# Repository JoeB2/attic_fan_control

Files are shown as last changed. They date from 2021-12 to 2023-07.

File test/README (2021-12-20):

This directory is intended for PlatformIO Unit Testing and project tests.

Unit Testing is a software testing method by which individual units of
source code, sets of one or more MCU program modules together with associated
control data, usage procedures, and operating procedures, are tested to
determine whether they are fit for use. Unit testing finds problems early
in the development cycle.

More information about PlatformIO Unit Testing:
- https://docs.platformio.org/page/plus/unit-testing.html

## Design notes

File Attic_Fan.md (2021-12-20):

Problem:
Turn on/off attic fan in the summer.  Use attic temp, Web Page, and outside sensor to determine whether fan is on or off.

Considerations:
Fan On/Off (use 5min increment timmer)

Fan on if Attic above some threshold temp : 110f

Fan never on - inside temp <75 and Delta Inside-Outside > 20

Fan on if delta inside-outside > 10f
Fan on if delta attic-outside > 50f

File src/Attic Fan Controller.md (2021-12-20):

## Introduction

This ESP8266 web based application is intended to allow a user to set temperature difference thresholds, between 3 temperature probes, which will determine whether the attic fan will turn on or off.

## Architecture

The ESP8266 is an ESP01-1M.  The MCU hosts four web pages, readings, settings, wifi, and OTA (Over the Air firmware updates).  WebSockets are used to manage communication between the MCU and the web pages.  Web pages are hosted on the user's local wifi network, using provided ip4 and ssid/password information using the wifi web form.  Additionally the MCU simultaneously hosts an access point ("AtticFan WiFi: 10.0.1.23") on a fixed ip at 10.0.1.23.  The access point allows the user to set ip4 information for the local wifi network, read sensor and fan status values, set fan activation thresholds, and update the firmware over wifi - the same as the local WiFi ip would.  The Attic and inside temperature probes are dallas DS18B20 probes using the "one wire" protocol.  The outside probe is a BME280 using the i2c protocol and it transmits its values using the proprietary ESPNOW protocol.  Rem,ote sensor values are sent every "Remote Sensor Check-In Minutes" which is configurable on the setting web page.

Threshold and wifi values are stored in non volatile memory using JSON strings.  The string format is as follows:

### atticFan JSON:
***[{"t1":75.2,"t2":75.4,"t3":74.6,"p3":29.25,"h3":32,"dp3":42,"a3":1448,"vcc":3.0,"atticEpochTime":1638658867,"fanOn":false,"fanOnMs":96},{"attic_on":150,"attic_off":0,"AID_on":0,"AID_off":0,"AOD_on":0,"AOD_off":0,"IOD_on":7,"IOD_off":3,"fanEnabled":false,"delayMs":0,"sleepTIMEus":15000000}]***

###  WiFi JSON:
***{"ssid":"mySSID","pwd":"myPassword","isDHCP":false,"ip":"10.9.8.07","gw":"10.9.8.128","mask":"255.255.255.128"}***

The JSON strings can me modified using the associated web pages and uploaded over the connected wifi network.  

## Operation
  Network Setup
    1) after startup of the attic MCU (micro controller unit) connect to the WiFi access point "AtticFan WiFi: 10.0.1.23".
    2) Point your web browser to: http://10.0.1.23/wifi
        Note: lower case wifi.
    3) Fill out the WiFi settings with the values for your local WiFi network and submit, which will save  the values to non volatile memory (SPIFFS) in a JSON string.
    4) After the WiFi settings are saved the MCU will attempt to re initiate connection to local WiFi provided when filling out the WiFi web form.  An MCU restart is typically not required.

## Home readings web page (http://ip/)

Temperature are provided for all three temperature probes.  The outside probe also provided humidity and barometric pressure reading.  The Attic MCU uses the outside prob's val;ues to calculate outside dew point and density altitude.  The reading page provides "Fan On Timer" values and to disable or active the system.

## Settings (http://ip/settings)

Values are provided using the web form at: http://ip/settings, where ip is the local WiFi ip provided during step 1 of the Network Setup.  Alternatively you can use the Access Point ip, after connecting to the MCU's provided access point.
Settings "AOD, AID, IOD" are value of difference in temperature fahrenheit between temperature probes.  IOD_on (inside - outside = difference) turns on the fan if the difference between the inside temperature probe and the outside temperature probe is equal or greater than the value provided.  Similarly the fan will turn off if: there are no other fan on values whose thresholds have been met and the *inside temp probe* **-** *outside temp probe* **<** ***IOD_off***.  

Order of precedence for automating fan ***on***:
  Fan On:
    - Force Fan On Minutes
    - Fan On Attic Temp
    - IOD on
    - AID on
    - AOD on

Setting "fan System Enabled" to off will disable the fan.
Otherwise IOD off, AOD off, AID off, Attic Fan off temp will be honored with the first threshold met that doesn't conflict with ***any*** fan on threshold turning off the fan.  If no fan off threshold is set the fan will turn off when no "fan On" threshold is met.

Attic Sensor Check-In Seconds setting will change the frequency that the system looks at Attic and Inside temperature probe values and also the frequency that the settings are tested and sent to the web page.

Likewise the "Remote Sensor Check-In Minutes" setting will determine the frequency that the battery operated outside sensor wakes up and transmits the outside temperature.  Battery life will be extended with greater Remote Sensor Check-In values.

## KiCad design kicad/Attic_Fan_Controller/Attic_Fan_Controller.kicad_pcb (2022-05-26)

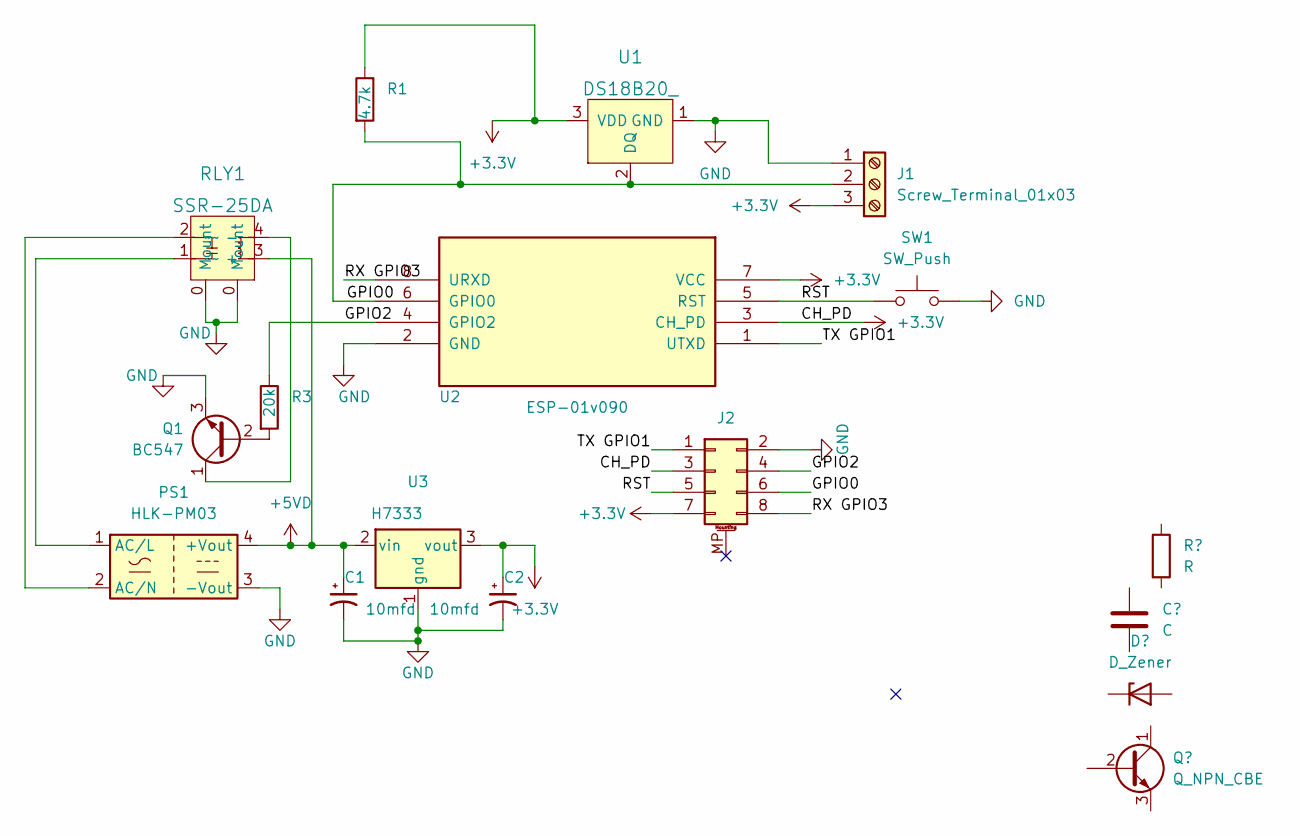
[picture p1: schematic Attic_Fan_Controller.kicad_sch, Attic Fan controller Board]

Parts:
C1, C2: 10mfd; CP_Radial_D4.0mm_P1.50mm
J1: Screw_Terminal_01x03; TerminalBlock_Phoenix_PT-1,5-3-5.0-H_1x03_P5.00mm_Horizontal
J2: Conn_02x04_Odd_Even_MountingPin; PinSocket_2x04_P2.54mm_Vertical
PS1: HLK-PM03; Converter_ACDC_HiLink_HLK-PMxx
Q1: BC547; TO-92_Inline
R1: 4.7k; R_Axial_DIN0207_L6.3mm_D2.5mm_P10.16mm_Horizontal
R3: 20k; R_Axial_DIN0207_L6.3mm_D2.5mm_P10.16mm_Horizontal
RLY1: SSR-25DA; SSR-25 DA; MPN 9007-05-00; Digi-Key_PN 306-1062-ND
SW1: SW_Push; SW_PUSH_6mm_H5mm
U1: DS18B20_; TO-92-3; MPN DS18B20+; Digi-Key_PN DS18B20+-ND
U2: ESP-01v090; ESP-01
U3: H7333; SOT-89-3

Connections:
+3V3: C2.1, J1.3, J2.3, J2.7, R1.1, U1.3 (VDD), U2.3 (CH_PD), U2.7 (VCC), U3.3 (vout); also elsewhere on the board
+5VD: C1.1, PS1.4 (+Vout), RLY1.3 (+), U3.2 (vin)
/GPIO0: J1.2, J2.6, R1.2, U1.2 (DQ), U2.6 (GPIO0)
/GPIO2: J2.4, R3.1, U2.4 (GPIO2); also elsewhere on the board
/RST: J2.5, SW1.1, U2.5 (RST)
/RX GPIO3: J2.8, U2.8 (URXD)
/TX GPIO1: J2.1, U2.1 (UTXD)
GND: C1.2, C2.2, J1.1, J2.2, PS1.3 (-Vout), Q1.3 (E), RLY1.0 (Mount), SW1.2, U1.1 (GND), U2.2 (GND), U3.1 (gnd)
unnamed: PS1.1 (AC/L), RLY1.1 (~~)
unnamed: PS1.2 (AC/N), RLY1.2 (~~)
unnamed: Q1.1 (C), RLY1.4 (-)
unnamed: Q1.2 (B), R3.2

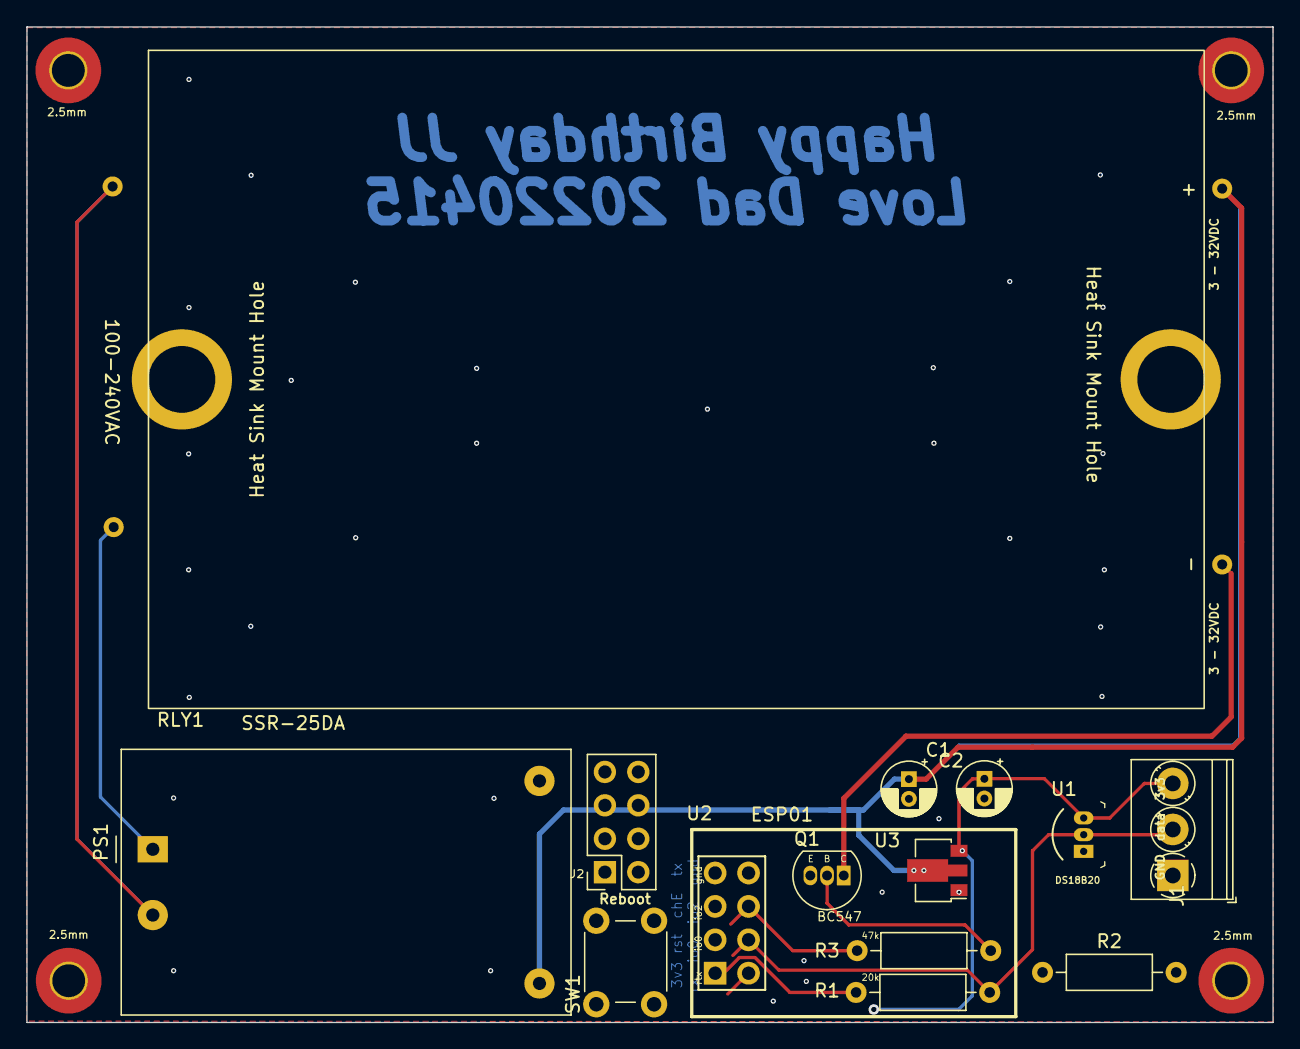
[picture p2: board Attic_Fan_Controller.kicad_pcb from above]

Board: 2 copper layers, 94.7 x 75.7 mm, 18 parts (0 on the bottom side), 12 nets.

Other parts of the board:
2.5mm, 2.5mm#2, 2.5mm#3, 2.5mm#4: MountingHole_2.5mm_Pad_TopBottom
R2: 10k; R_Axial_DIN0207_L6.3mm_D2.5mm_P10.16mm_Horizontal

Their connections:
+3V3: R2.1; also elsewhere on the board
/GPIO2: R2.2; also elsewhere on the board

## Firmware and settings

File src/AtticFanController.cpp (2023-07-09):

#include <Arduino.h>
/*
  Attic Fan Controller

  Purpose:  Regulate an attic fan's on and off.  The fan will move air from the hallway into the attic
            and the attic air will consequently move out of the attic's roof and eves vents.

  What this does: Measurement of attic temperature, hallway temperature, and outside temperature are calculated
            fed into a function to determine whether to turn the fan on or turn the fan off.

  The Fan ON/OFF function: uses the three temperatures (Attic, Inside, Outside) and compares them and
            their differences to values provided by you to automate the attic fan during the hot summer days.

  Function: There are four hosted web pages: 1. Main page http://ip showing status and providing you with a fan override
            function.  2. A settings page http://ip/settings where you can enter temperature difference values that will trigger
            Fan ON/OFF activity.  3. A WiFi settings page http://ip/wifi where local WiFi information can be entered.
            4. A over the air OTA page http://ip/update where firmware or static storage information can be uploaded to
            the ESP01 attic MCU.
            Stored in the MCU's static memory are two JSON strings named: atticFan and creds.  They host the fan's
            operational temperature deltas and the WiFi credential information, respectively.

            A value of zero "0" for a given Fan operational parameter disables that parameter.
  NOTE:     The parameters entered on the http://ip/settings page denote the temperature difference in degrees Fahrenheit.

            example: AOD on value: "Attic Outside Delta on" a value of 10 indicates you want the fan on
            if Attic Temp minus Outside temp is greater than or equal to 10 degrees f.  Absolute temperature settings are
            specifically labeled as such.
            int(4), uint(4), uint32(4), long(4), uLong(4), uLongLong(8), short(2), ushort(2), float(4), double(8)

  Primary Parts:
            ESP8266 - ESP01, 2ea DS18b20, relay, PCB/3.3vdc regulator; 
*/

#define dbg
#ifdef dbg
  u32 ms=millis();
  #define trace Serial.printf("%i %lums, ", __LINE__, millis()-ms);ms=millis();Serial.flush();
#else
  #define trace ;
#endif
#define dbg2

#include <LittleFS.h>
#include <ESP8266WiFi.h>
//#include <WiFiClientSecure.h>
#include <ESP8266mDNS.h>
#include <espnow.h>
#include <string>

// OTA
#include <AsyncElegantOTA.h>

// Web Server
#include <ESPAsyncWebServer.h>
#include <ESPAsyncTCP.h>
#include <index.h>

// DS18B20
#include <OneWire.h>
#include <DallasTemperature.h>

// bit macros
#define SET_BIT(x, pos) (x |= (1U << pos))

#define CLEAR_BIT(x, pos) (x &= (~(1U<< pos)))
#define CHECK_BIT(x, pos) (x & (1UL << pos) )

// Standard settings for compile
#define SSR_PIN 5       // ESP01: 3
#define ALTITUDE 394    // MSL altitude at JJ's house
#define WiFiChannel 7   // ESP NOW requires all peers are on the same channel
#define ONE_WIRE_BUS 4  // ESP01: 0

const char AP_SSID[]   = "AtticFan AP: 10.17.17.23"
         , HOST_NAME[] = "JJ's Attic Fan Controller"; // max length 32

const DeviceAddress // DS18B20 Addresses
          T1={0x28, 0x9C, 0x50, 0xF4, 0x3E, 0x19, 0x01, 0x12}  // white mark : Attic ...0x12
        , T2={0x28, 0x31, 0xCA, 0xC7, 0x3E, 0x19, 0x01, 0xCE}; // Corded     : Inside ...0xCE

// ESPNOW
//u8 peer[]       = {0xFF,0xFF,0xFF,0xFF,0xFF,0xFF};   // MAC: MultiCast"
u8 remote_Mac[]       = {0xDC,0x4F,0x22,0x49,0x59,0x15};   // MAC: MultiCast"

float tSync[] = {-1.2,0.55}; // attic, inside : sync DS18B20 temps to BME280

u32 startMillis=millis(); // loop sensor read delay
u32 last_Remote_Contact_millis=millis(); //

AsyncWebServer webServer(80);
AsyncWebSocket webSock("/");

OneWire oneWire(ONE_WIRE_BUS);
DallasTemperature sensors(&oneWire);

IPAddress  // soft AP IP info
          ip_AP(10,17,1,23)
        , ip_GW(10,17,0,125)
        , ip_AP_GW(10,17,1,23)
        , ip_subNet(255,255,255,128);

  struct {
//      std::string ssid = "myWiFi";     // max 342 characters
//      std::string pwd  = "secretPWD";  // max 64 characters
//      std::string host = HOST_NAME;
//      bool isDHCP      = false;
//      std::string ip   = "198.162.123.117";
//      std::string gw   = "198.162.123.117";
//      std::string mask = "255.255.255.128";
//      bool isDHCP      = false;
      std::string ssid = "JRJAG";     // max 342 characters
      std::string pwd  = "GeorgeTheDogy";  // max 64 characters
      std::string host = HOST_NAME;
      bool isDHCP      = true;
      std::string ip   = "10.137.17.23";
      std::string gw   = "10.137.17.1";
      std::string mask = "255.255.255.128";
      bool updated     = 0;

      std::string toStr(){
        char s[146];
        size_t n;
        n = sprintf(s, "{\"src\":\"mcuNetwork\",\"ssid\":\"%s\",\"pwd\":\"%s\",\"isDHCP\":%hhu,\"ip\":\"%s\",\"gw\":\"%s\",\"mask\":\"%s\",\"updated\":%hhu}"
        , ssid.c_str(), pwd.c_str(), isDHCP?1:0, ip.c_str(), gw.c_str(), mask.c_str(), updated);
        return(std::string(s, n));
      };
  } network;

typedef struct remote_Data{
  int temp;
  u32 press;
  u32 humid;
  u64 sleep_us = 4000000;
  u16 vcc;

  String toStr(){
    char c[120];
    int n = sprintf(c, "{\"temp\":%i,\"press\":%u,\"humid\",:%u,\"vcc:%hu,\"sleep_us\":%llu}"
      , temp, press, humid, vcc, sleep_us);
    c[n]=0;
    return String(c);
  }
}remote_data_t;
remote_data_t now_Msg;

 struct{
  float t1;		                  // attic
  float t2;	                    // inside
  float t3;	                    // outside - remote sensor temp
  u32 p3;                       // outside air pressure inHg
  u32 h3;	                      // humidity outside
  u32 vcc;	                    // battery voltage Vcc at remote sensor
  bool fanOn;	                  // fan on/off indicator
  int fanOnMs=0;         
  byte attic_on;                // Attic temp to force Fan ON: 0 to disable (Master Override)
  byte attic_off;               // Attic temp to turn fan OFF: 0 to dissable
  byte inside_off=70;           // Fan is off if t2 (inside) is below 70 (default) degrees;
  byte AID_on;                  // Attic - Inside temp delta for fan ON: 0 to dissable   (precedence 3)
  byte AID_off;                 // Attic - Inside temp delta for fan OFF: 0 to dissable
  byte AOD_on;                  // Attic - Outside temp delta for fan ON: 0 to dissable  (precedence 2)
  byte AOD_off;                 // Attic - Outside temp delta for fan OFF: 0 to dissable
  byte IOD_on;                  // Inside - Outside temp delta for fan ON: 0 to dissable (precedence 1)
  byte IOD_off;                 // Inside - Outside temp delta for fan OFF: 0 to dissable
  bool systemEnabled;           // true: ok to turn on fan; // logic simplifies some c++ later on
  unsigned long delayMs = 15000;// how often are attic temps checked in milliseconds
  u64 sleep_us = 2*60*1e6+2;    // default: 2mins 2us: remote sensor deepSleep time
  bool updated = false;

    std::string mcuMain(){      // make JSON string: #1 Readings, #2 Settings
      char c[275];
      size_t n;
      n = sprintf(c, "{\"src\":\"mcuMain\",\"t1\":%# 6.1f,\"t2\":%# 6.1f,\"t3\":%# 6.1f,\"p3\":%u,\"h3\":%u,\"vcc\":%hu,\"fanOn\":%hhu,\"fanOnMs\":%i,\"systemEnabled\":%hhd,\"sleep_us\":%llu}"
      , t1, t2, t3, p3, h3, vcc, fanOn?1:0, fanOnMs, systemEnabled?1:0, sleep_us);

      return(std::string(c, n));
    }
    std::string mcuSettings(){ // make JSON string: #1 Readings, #2 Settings
      char c[285];
      size_t n;
      // we send this json using webSock to the settings web page
      n = sprintf(c, "{\"src\":\"mcuSettings\",\"fanOn\":%hhu,\"attic_on\":%hhu,\"attic_off\":%hhu,\"inside_off\":%hhu,\"AID_on\":%hhu,\"AID_off\":%hhu,\"AOD_on\":%hhu,\"AOD_off\":%hhu,\"IOD_on\":%hhu,\"IOD_off\":%hhu,\"systemEnabled\":%hhu,\"delayMs\":%lu,\"sleep_us\":%llu,\"updated\":%hhu}"
      , fanOn?1:0, attic_on, attic_off, inside_off, AID_on, AID_off, AOD_on, AOD_off, IOD_on, IOD_off, systemEnabled?1:0, delayMs, sleep_us, updated);

      return(std::string(c, n));
    }
    // atticFan struct: true==turn on fan
    bool setFanOn(){
        // 1)systemEnabled, 2)timmer, 3)inside_off -> order of precedence
        if(systemEnabled==0){fanOn=0;return 0;}
        if(fanOnMs){fanOn=1;return 1;}
        if(inside_off && t2 <= inside_off){fanOn=0;return 0;}

        // fan OFF tests: is there an off setting that is active?
        if(IOD_off && t2-t3<IOD_off)fanOn=0;
        if(AOD_off && t1-t3<AOD_off)fanOn=0;
        if(AID_off && t1-t2<AID_off)fanOn=0;
        if(attic_off && t1<attic_off)fanOn=0;

        // turn off fan, if there is not an "Off Setting" that has been set else leave as is
        fanOn &= (AID_off | AOD_off | IOD_off | attic_off | inside_off);

        // NOTE: On settings override conflicting (AID, AOD, IOD) temp off settings
        // fanOn ON checks: Should the fan be turned on because of a setting?  else leave as is
        fanOn |= ( (AOD_on&(t1-t3 >= AOD_on)) | (AID_on&(t1-t2 >= AID_on)) | (IOD_on&(t2-t3 >= IOD_on)) | (attic_on&(t1>=attic_on)));
        return fanOn;
    }
  }atticFan;

  /******  PROTOTYPES  *******/
  // web
  void notFound(AsyncWebServerRequest *request);
  void onWsEvent(AsyncWebSocket * server, AsyncWebSocketClient * client, AwsEventType type, void * arg, uint8_t *data, size_t len);

	// ESP_NOW
	void OnDataSent(uint8_t *mac_addr, uint8_t sendStatus);
	void OnDataRecv(uint8_t * mac, uint8_t *incomingData, uint8_t len);

  void initAtticFanStruct(); // load struct atticFan from LittleFS
  void setAtticFanStruct(const std::string &s); // set struct atticFan's differential switching values from WebSock string
  bool saveAtticFanStruct(); // save struct atticFan's JSON string in LittleFS
  bool initWiFi(); // load struct creds from LittleFS
  bool saveWiFi(); // save struct creds JSON string in LittleFS 
  void initWiFi(const std::string &s); // load struct creds from WebSock string
  wl_status_t wifiConnect(WiFiMode_t m);
  IPAddress str2IP(const std::string &s);
  String mac2string(const uint8_t *mac);
  std::string valFromJson(const std::string &json, const std::string &element);// Parse JSON string


  void setup() {
#ifdef dbg
    Serial.begin(74880); // initial boot message is at 74880
    delay(500);
    Serial.printf("\n%i\n", __LINE__);Serial.flush();
#endif
    sensors.begin();
    LittleFS.begin();     // store WiFi Creds
trace
    initWiFi();           // get WiFi credentials from LittleFS
    initAtticFanStruct(); // get temp settings
trace

    wifi_set_phy_mode(PHY_MODE_11B); // high power wifi
    if(wifiConnect(WIFI_STA) != WL_CONNECTED)wifiConnect(WIFI_AP);
		pinMode(SSR_PIN, OUTPUT);
    digitalWrite(SSR_PIN, 0);
trace

		esp_now_init();
		esp_now_set_self_role(ESP_NOW_ROLE_COMBO);
		esp_now_register_send_cb(OnDataSent);
		esp_now_register_recv_cb(OnDataRecv);
		esp_now_add_peer(remote_Mac, ESP_NOW_ROLE_COMBO, WiFiChannel, NULL, 0);
trace

		// init Websock
		webSock.onEvent(onWsEvent);
		webServer.addHandler(&webSock);
trace

		// Web Pages
		webServer.onNotFound(notFound);
    if(WiFi.softAPIP().toString() == "(IP unset)"){
      webServer.on("/"         , HTTP_GET, [](AsyncWebServerRequest *request){request->send_P(200, "text/html", MAIN);});
      webServer.on("/settings" , HTTP_GET, [](AsyncWebServerRequest *request){request->send_P(200, "text/html", SETTINGS);});
      webServer.on("/wifi"     , HTTP_GET, [](AsyncWebServerRequest *request){request->send_P(200, "text/html", NETWORK);});
    }
    else {webServer.on("/"     , HTTP_GET, [](AsyncWebServerRequest *request){request->send_P(200, "text/html", NETWORK);});}

    ESP.wdtFeed();
		AsyncElegantOTA.begin(&webServer);    // Start ElegantOTA
trace
		webServer.begin();
trace
		startMillis=millis()-atticFan.delayMs; // get temps immediately after startup
  }
  void loop() {
    if(millis()-startMillis > atticFan.delayMs){
trace

        sensors.requestTemperatures();
        atticFan.t1 = sensors.getTempF(T1)+tSync[0];
        atticFan.t2 = sensors.getTempF(T2)+tSync[1];
trace

        ESP.wdtFeed();

        /** Timer Section **/
        if(atticFan.fanOnMs)atticFan.fanOnMs-=(millis()-startMillis);
        if(atticFan.fanOnMs>120*60000)atticFan.fanOnMs=120*60000;// 2hr max timer
        if(atticFan.fanOnMs<(int)atticFan.delayMs)atticFan.fanOnMs=0;
        atticFan.setFanOn();
        /** END Timer Section **/

        digitalWrite(SSR_PIN, atticFan.fanOn);
        webSock.textAll(atticFan.mcuMain().c_str());
        ESP.wdtFeed();
trace

        /** LastRemoteContact Section **/
        // if missed last 3 remote contacts set sensor readings to zero
        if(millis() - last_Remote_Contact_millis > 3*atticFan.sleep_us)
        {atticFan.t3=0;atticFan.p3=0;atticFan.h3=0;atticFan.vcc = 0;}
        /** END lastRemoteContact **/

        startMillis=millis();
    }
  }
  void notFound(AsyncWebServerRequest *request){request->send_P(200, "text/html", MAIN);}
  //**********************************************************************
  void onWsEvent(AsyncWebSocket * server, AsyncWebSocketClient * client, AwsEventType type, void * arg, uint8_t *data, size_t len){
    if(type == WS_EVT_CONNECT){client->ping();webSock.cleanupClients();}
    if(type == WS_EVT_DISCONNECT){client->close();webSock.cleanupClients();}
//**************
    if(type != WS_EVT_DATA)return;
      AwsFrameInfo * info = (AwsFrameInfo*)arg;
      if(info->final && !info->index && info->len == len){
        if(info->opcode != WS_TEXT)return;
      }
      data[len]=0; // null terminate the char[]
      std::string s((char*)data, len);
      std::string src = valFromJson(s, "src");
      std::string what = valFromJson(s, "what");

#ifdef dbg
    Serial.printf("\n%i ws_in: %s\n", __LINE__, s.c_str());
#endif
      if(src=="main"){
        if(what=="system"){
          atticFan.systemEnabled = ::atoi(valFromJson(s, "system").c_str());
        }
        if(what=="timer"){
          atticFan.fanOnMs = ::atoi(valFromJson(s, "fanOnMs").c_str());
        }
        atticFan.setFanOn();
        digitalWrite(SSR_PIN, atticFan.fanOn);
        client->text(atticFan.mcuMain().c_str());
      }
      if(src=="settings"){
          if(what=="submit"){
            setAtticFanStruct(s);
            atticFan.updated = saveAtticFanStruct();
          }
          if(what=="system"){
            atticFan.systemEnabled = ::atoi(valFromJson(s, "systemEnabled").c_str());
          }
          digitalWrite(SSR_PIN, atticFan.setFanOn());
#ifdef dbg
  Serial.printf("\n%i %s\n", __LINE__, atticFan.mcuSettings().c_str());
#endif
          client->text(atticFan.mcuSettings().c_str());
          atticFan.updated = false;
        }
      if(valFromJson(s, "src")=="network"){
        if(what=="reboot")ESP.restart();
        if(what=="submit"){
          initWiFi(s); // <-- updated, but no reboot yet
          network.updated = saveWiFi();
        }
        client->text(network.toStr().c_str()); // include "updated" value
      }
#ifdef dbg2
    Serial.printf("\n%i mcuMain: %s\n\nmcuSettings: %s\n\n"
            , __LINE__, atticFan.mcuMain().c_str(), atticFan.mcuSettings().c_str());
#endif
  }
  void OnDataRecv(uint8_t * mac, uint8_t *incomingData, uint8_t len){
trace
      memcpy(&now_Msg, incomingData, sizeof(now_Msg));
trace
#ifdef dbg
      Serial.printf("\n%i %s :Remote MAC: %s\t Local MAC: %s\n\n", __LINE__, __FUNCTION__, mac2string(mac).c_str(), WiFi.macAddress().c_str());
      Serial.printf("NOW IN MSG: %s\n", now_Msg.toStr().c_str());Serial.flush();
#endif
trace
      atticFan.t3  = .018 * now_Msg.temp + 32.0;
      atticFan.p3  = now_Msg.press; // pressure x 100
      atticFan.h3  = now_Msg.humid; // humidity x 100
      atticFan.vcc = now_Msg.vcc;   // vcc x 1000
trace
      last_Remote_Contact_millis=millis(); // used to decide whether the remote may have a communication problem

      webSock.textAll(atticFan.mcuMain().c_str());// send updated sensor data

      if(now_Msg.sleep_us != atticFan.sleep_us)
              esp_now_send(remote_Mac, (u8*) &atticFan.sleep_us, 8);
trace
      delay(25);
	}
  void OnDataSent(uint8_t *mac_addr, uint8_t sendStatus) {
#ifdef dbg
  Serial.printf("%i NOW Delivery %s. AtticFan.sleep_us: %llu\n\n", __LINE__, sendStatus?"ERROR":"SUCCESS", atticFan.sleep_us);Serial.flush();
#endif
  }
  void initAtticFanStruct(){
    File f = LittleFS.open("/settings", "r");
    if(f){
          const std::string s = f.readString().c_str();
          f.close();
          setAtticFanStruct(s);
    }
  }
  void setAtticFanStruct(const std::string &s){
#ifdef dbg
  Serial.printf("\n%i %s\n%s\n\n", __LINE__, __FUNCTION__, s.c_str());Serial.flush();
#endif
        atticFan.attic_on        = std::stoi(valFromJson(s, "attic_on"));
        atticFan.attic_off       = std::stoi(valFromJson(s, "attic_off"));
        atticFan.inside_off      = std::stoi(valFromJson(s, "inside_off"));
        atticFan.AID_on          = std::stoi(valFromJson(s, "AID_on"));
        atticFan.AID_off         = std::stoi(valFromJson(s, "AID_off"));
        atticFan.AOD_on          = std::stoi(valFromJson(s, "AOD_on"));
        atticFan.AOD_off         = std::stoi(valFromJson(s, "AOD_off"));
        atticFan.IOD_on          = std::stoi(valFromJson(s, "IOD_on"));
        atticFan.IOD_off         = std::stoi(valFromJson(s, "IOD_off"));
        atticFan.systemEnabled   = std::stoi(valFromJson(s, "systemEnabled"))?1:0;
        atticFan.delayMs         = std::stoul(valFromJson(s, "delayMs"));
        atticFan.sleep_us        = std::stoull(valFromJson(s, "sleep_us"));
#ifdef dbg
  Serial.printf("%i %s\n\t%llu\n", __LINE__, s.c_str(),atticFan.sleep_us);
#endif
  }
  bool saveAtticFanStruct(){
      File f = LittleFS.open(F("/settings"), "w");
      if(f){
        f.print(atticFan.mcuSettings().c_str());
        f.close();
        return true;
    }
    else{return false;}
  }
  bool initWiFi(){
        File f = LittleFS.open("/network", "r");
        if(f){
               const std::string s = f.readString().c_str();
                f.close();
                initWiFi(s);
                return(true);
        }
        return(false);
  }
  void initWiFi(const std::string &s){
#ifdef dbg
  Serial.printf("\n%i : %s\n", __LINE__, s.c_str());
#endif
    network.ssid   = valFromJson(s, "ssid");
    network.ip     = valFromJson(s, "ip");
    network.pwd    = valFromJson(s, "pwd");
    network.isDHCP = valFromJson(s, "isDHCP")=="1";
    network.gw     = valFromJson(s, "gw");
    network.mask   = valFromJson(s, "mask");
  }
  // saveWiFi() resets "updated" flag before the save
  bool saveWiFi(){
#ifdef dbg
  Serial.printf("\n%i : %s : %s\n", __LINE__, __FUNCTION__, network.toStr().c_str());
#endif
    network.updated=0; // we never save "updated's" state
    File f = LittleFS.open(F("/network"), "w");
    if(f){
      f.print(network.toStr().c_str());
      f.close();
      return 1;
    }
    else
      return 0;
  }
//Connect WiFi
  wl_status_t wifiConnect(WiFiMode_t m){
    WiFi.disconnect(true);
    WiFi.softAPdisconnect(true);
    WiFi.softAP(AP_SSID);

#ifdef dbg2
  // WIFI_OFF = 0, WIFI_STA = 1, WIFI_AP = 2, WIFI_AP_STA = 3
  std::string mode;
  switch(m){case 0: mode="OFF";case 1: mode="STA"; case 2: mode="AP"; case 3: mode="AP_STA";}
  Serial.printf("\n%i: WiFi_Mode: %s : %s\n",__LINE__, mode.c_str(), network.toStr().c_str());
#endif

    WiFi.mode(m);  // WIFI_AP_STA,WIFI_AP; WIFI_STA;
    switch(m){
        case WIFI_STA:
            WiFi.enableAP(false);
            WiFi.enableSTA(true);
            WiFi.setHostname(network.host.c_str());
            if(!network.isDHCP)WiFi.config(str2IP(network.ip), str2IP(network.gw), str2IP(network.mask));
            WiFi.begin(network.ssid.c_str(), network.pwd.c_str(), WiFiChannel);
          break;
        case WIFI_AP:
            WiFi.enableSTA(false);
            WiFi.enableAP(true);
            WiFi.config(ip_AP, ip_AP_GW, ip_subNet);
            WiFi.softAPConfig(ip_AP, ip_AP_GW, ip_subNet);
            WiFi.softAP(AP_SSID);//, "", 7, false, 4);
            WiFi.channel(WiFiChannel);
            WiFi.begin();
          break;
        case WIFI_AP_STA:
            delay(25);
            WiFi.hostname("Attic Fan Controller");
            if(!network.isDHCP)
              WiFi.config(str2IP(network.ip), str2IP(network.gw), str2IP(network.mask));
            WiFi.softAPConfig(ip_AP, ip_AP_GW, ip_subNet);
            WiFi.softAP(AP_SSID, "", 3, false, 4);
            WiFi.begin(network.ssid.c_str(), network.pwd.c_str(), WiFiChannel);
          break;
        case WIFI_OFF: return(WiFi.status());
    }
    WiFi.setOutputPower(20.5);  // range: 0dbm - 20.5dbm

#ifdef dbg2
  Serial.printf("%i networkToStr(): %s\n",__LINE__, network.toStr().c_str());Serial.flush();
#endif

    unsigned long startup = millis();
#ifdef dbg
            Serial.println("\n");
#endif
    while(WiFi.status() != WL_CONNECTED){
      ESP.wdtFeed();
      delay(750);
#ifdef dbg
      Serial.print(".");
#endif
      if(millis() - startup >= 15000) break;
    }
#ifdef dbg
      Serial.print("\n\n");
#endif
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

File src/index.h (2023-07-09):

// pgm_read_byte() bug Stack Dumps: https://github.com/esp8266/Arduino/issues/3140 
#undef pgm_read_byte
#define pgm_read_byte(addr)                                                             \
(__extension__({                                                                        \
    PGM_P __local = (PGM_P)(addr);  /* isolate varible for macro expansion */           \
volatile ptrdiff_t __offset = ((uint32_t)__local & 0x00000003); /* byte aligned mask */ \
    const uint32_t* __addr32 = (const uint32_t*)((const uint8_t*)(__local)-__offset);   \
    uint8_t __result = ((*__addr32) >> (__offset * 8));                                 \
    }))
// END pgm_read_byte()

const char MAIN[] PROGMEM =  R"=====(
<!DOCTYPE html>
<html>
    <head>
        <meta name="viewport" content="width=device-width, initial-scale=1" />
        <link
            rel="stylesheet"
            href="https://use.fontawesome.com/releases/v5.7.2/css/all.css"
            integrity="sha384-fnmOCqbTlWIlj8LyTjo7mOUStjsKC4pOpQbqyi7RrhN7udi9RwhKkMHpvLbHG9Sr"
            crossorigin="anonymous"
        />
        <title>Attic Fan Controller</title>
        <style>
            @viewport{width:device-width;zoom:1.0;}
            @-ms-viewport {width: device-width ;}
            html{
                font-family: Arial;
                display: inline-block;
                margin: 0px auto;
                text-align: left;
                min-width: 544px;
                min-height:777px;
                background-color: dodgerblue;
            }
            h2 {
                font-size: 4.0vw;
                text-align: center;
            }
            h3 {
                font-size: 2.8vw;
                font-weight: bold;
                text-align: center;
                background-color: rgb(255,255,255);
                color: blue;
                vertical-align: top;
                margin-top:0px;
            }
            .help {
                border: 0;
                line-height: 3.5vw;

                padding: 0 1vw;
                text-align: center;
                font-weight:bold;
                font-size: 2.2vw;

                cursor: pointer;
                background-color: rgb(255, 255, 255);
                box-shadow: inset 1vw 1vw 1vw rgba(255, 255, 255, 0.6),
                    inset -.3vw -.25vw .3vw rgba(0, 0, 0, 0.6);

                border:19vw;

                margin-left:.3vw;
                margin-top: 4vw;
                padding: 1vw;

                width:67.9vw;
                margin-inline: 1vw;
            }
            .vcc {
                color: #242121;
                font-weight: bold;
                font-family: Verdana;

                text-align: center;
                vertical-align: top;
                padding-left: 1vw;
                padding-top: -1vw;
                font-size: 2.5vw;
                grid-column:5;
                grid-row:1/2;
            }
            .blink {
                animation: blinker 1.9s linear infinite;
                color: #a81a1a;
                font-weight: bold;
                font-family: Verdana;

                padding-left: 1vw;
                font-size: 2.5vw;
                grid-column:5;
                grid-row:1/2;
            }
            @keyframes blinker {
                99% {
                    opacity: 0;
                }
            }
            .sensors-grid{
                display:grid;
                grid-template-columns:24.5vw 12.3vw 20vw 13vw;
                grid-template-rows: 6vw 4vw 4vw 4vw 7vw;

                box-sizing: border-box;
                width: min(100%, 72.5vw);
                min-width: 39vw;
                height: 25vw;

                margin-left: 5vw;
                margin-right: 5vw;

                background-color: #ced3c7;
                justify-items: left;

                padding: 1.3vw 2.3vw;

                font-size:2.8vw;
                font-weight: bold;
            }
            .status-grid{
                display:grid;
                grid-template-columns:7vw 18vw 15vw 17vw 8vw;
                grid-template-rows: 4vw 9.5vw;

                box-sizing: border-box;
                width: min(100%, 72.5vw);
                min-width: 39vw;
                height: 16.5vw;

                margin-left: 5vw;
                margin-right: 5vw;

                background-color: #ced3c7;
                justify-items: center;

                padding: 1vw 2.8vw;

                font-size:2.5vw;
                font-weight: bold;
                text-align:center;
            }
            .time {
                grid-column: 4 / 5;
                color: blue;
                font-size:2.0vw;
            }
            .units {
                color: #a81a1a;
                font-weight: bold;
                font-family: Verdana;
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

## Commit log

2022-05-26 Project Completed
    [AtticFan_Controller.kicad_pcb, AtticFan_Controller.kicad_sch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]
2022-05-31 fixed inside_off parameter from json error
    [AtticFanController.cpp]
